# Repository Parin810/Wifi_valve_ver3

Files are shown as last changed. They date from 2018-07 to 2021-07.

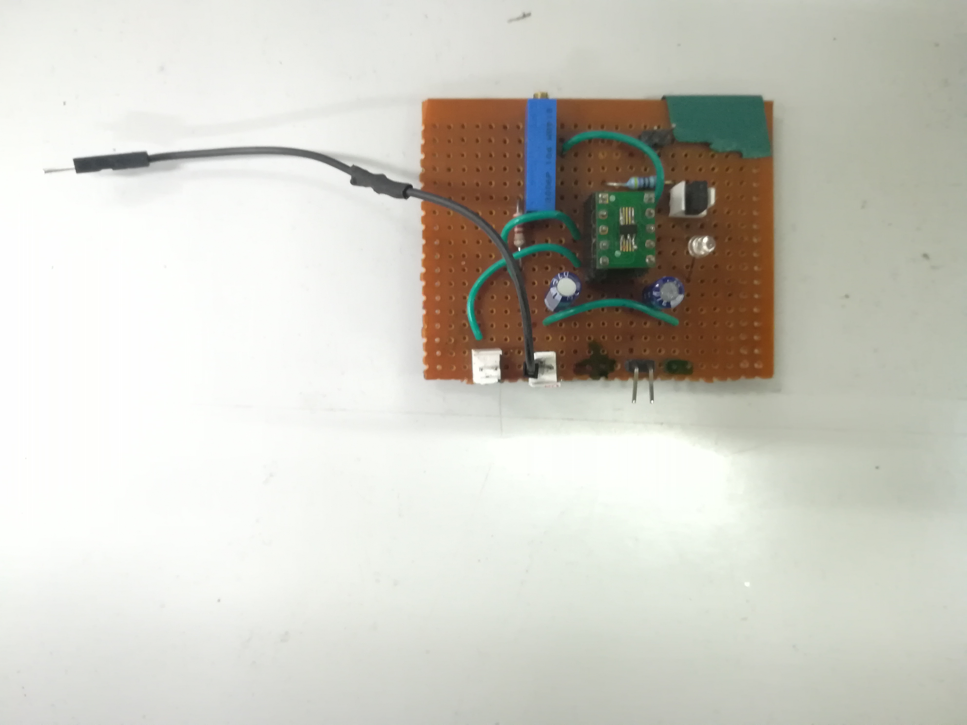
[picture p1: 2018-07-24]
IMG_20180724_112638.jpg

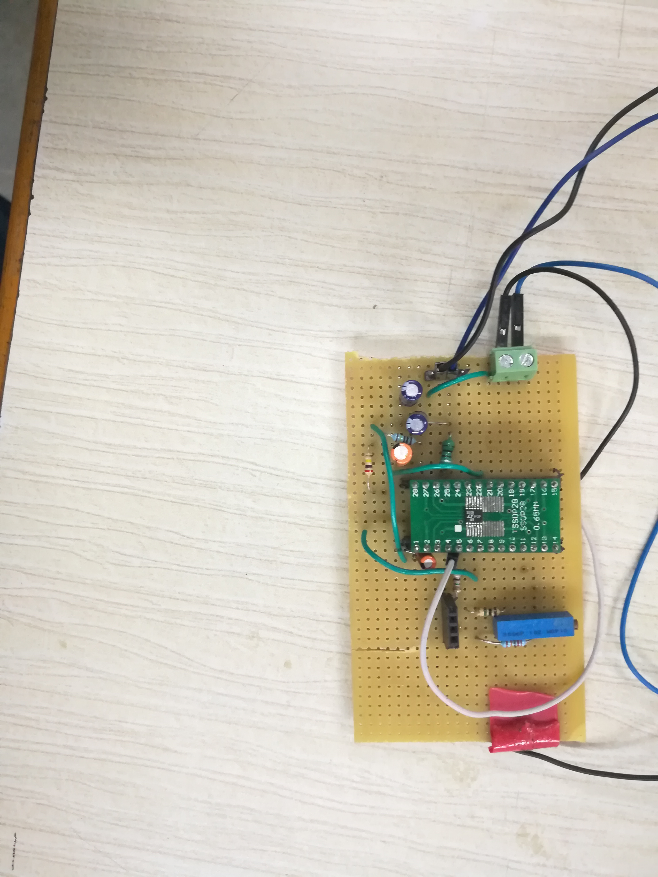
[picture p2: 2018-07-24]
IMG_20180724_134600.jpg

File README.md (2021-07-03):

### Solar Harvesting IoT based Irrigation valve:
This repo contains all the necessary hardware and software information about IoT/Wifi Actuator that has the following features:
1. ESP8266 as the controller/radio chip 
2. Uses MQTT as the communication protocol
3. BQ24210 or MCP73831 based solar harvestor
4. Uses Nodemcu custom build firmware
5. Auto modem sleep enabed (DTIM3,4,5)
6. The valve used is a latching solenoid 
7. DRV8832 as driver for latching solenoid
## Resources
The cheapst SOC that supports IEEE 802.11 standard
[ESP8266](https://tttapa.github.io/ESP8266/Chap04%20-%20Microcontroller.html)

Lua based firmware to simplify application programming
[Nodemcu - Lua](https://nodemcu.readthedocs.io/en/master/)

ESP8266 power consumption
[ESP8266 current profile](https://jeelabs.org/book/1526f/)

## Major Components Used 
(click to see datasheet)

[ESP8266-07](https://www.mikrocontroller.net/attachment/338570/Ai-thinker_ESP-07_WIFI_Module-EN.pdf)

LDO
[AP2112](https://www.diodes.com/assets/Datasheets/AP2112.pdf)

Lipo/ion charger
[MCP73831](http://ww1.microchip.com/downloads/en/DeviceDoc/20001984g.pdf)

Solar lipo/ion charger 
[BQ24210](http://www.ti.com/lit/ds/symlink/bq24210.pdf)

PMOS switch 
[PMV65XP](https://assets.nexperia.com/documents/data-sheet/PMV65XP.pdf)

## Loading LUA firmware
Download Nodemcu flasher from [here](https://github.com/nodemcu/nodemcu-flasher). for windows. For Linux use esptool.py (see repository for details)
Look at this [page](https://nodemcu.readthedocs.io/en/master/en/flash/) from nodemcu lua documentation

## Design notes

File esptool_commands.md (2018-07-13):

Use the follwoing command to flash the 2016 version of the firmware in the ESP8266 Board.

sudo python esptool.py --port /dev/ttyUSB0 write_flash 0x0000 nodemcu_integer_0.9.6-dev_20150704.bin 

Use the follwoing command to flash the 2018 version of the firmware in the ESP8266 Board.

sudo python esptool.py --port /dev/ttyUSB0 write_flash 0x3fc000 esp_init_data_default.bin

sudo python esptool.py --port /dev/ttyUSB0 write_flash 0x0000 nodemcu_master_18_modules_2018_integer.bin

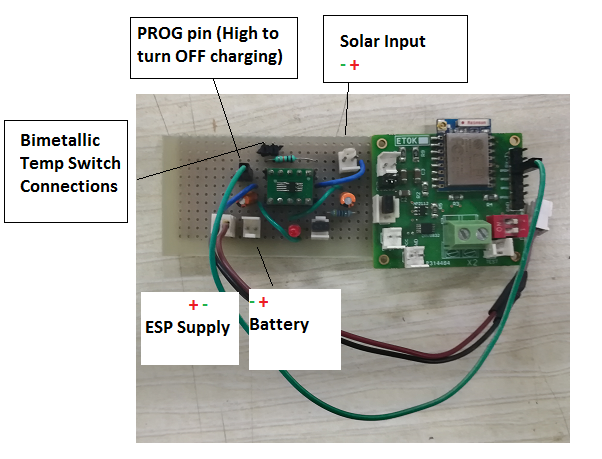
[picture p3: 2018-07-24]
mcp73831_gpb_2.png

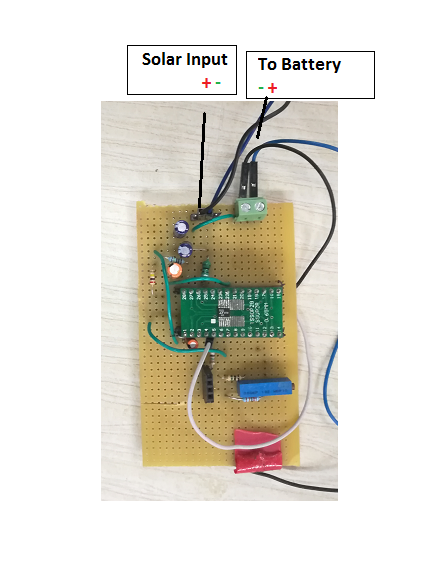
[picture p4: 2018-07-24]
LTC3105_gpb.png

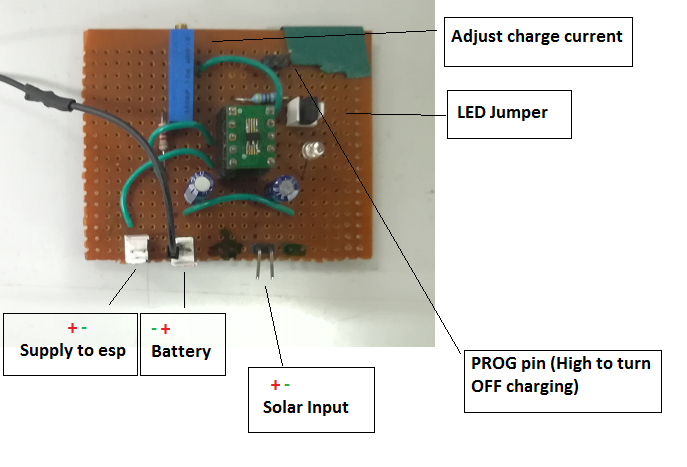
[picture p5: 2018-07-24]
mcp73831_gpb_1.png

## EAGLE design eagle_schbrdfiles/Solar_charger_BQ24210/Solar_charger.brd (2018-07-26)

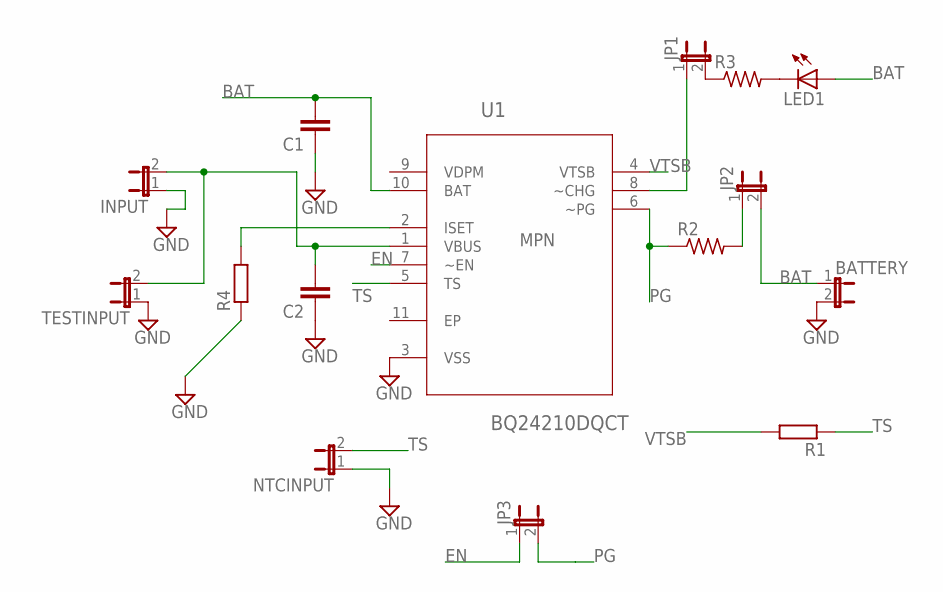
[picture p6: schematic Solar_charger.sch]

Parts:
BATTERY: JP1E; JP1
C1, C2: C2,5-3; C2.5-3
INPUT: JP1E; JP1
JP1, JP2, JP3: JP1E; JP1
LED1: LED5MM
NTCINPUT: JP1E; JP1
R1, R4: R-EU_0204/7; 0204/7
R2, R3: R-US_M1206; M1206
TESTINPUT: JP1E; JP1
U1: BQ24210DQCT; SON50P200X300X80-11N

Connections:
BAT: BATTERY.1, C1.2, JP2.2, LED1.A, U1.10 (BAT)
EN: JP3.1, U1.7 (~EN)
GND: BATTERY.2, C1.1, C2.1, INPUT.1, NTCINPUT.1, R4.1, U1.3 (VSS)
unnamed: C2.2, INPUT.2, TESTINPUT.2, U1.1 (VBUS)
unnamed: R4.2, U1.2 (ISET)
unnamed: JP2.1, R2.2
unnamed: LED1.K (C), R3.2
unnamed: JP1.1, U1.8 (~CHG)
unnamed: JP1.2, R3.1
PG: JP3.2, R2.1, U1.6 (~PG)
TS: NTCINPUT.2, R1.1, U1.5 (TS)
VTSB: R1.2, U1.4 (VTSB)

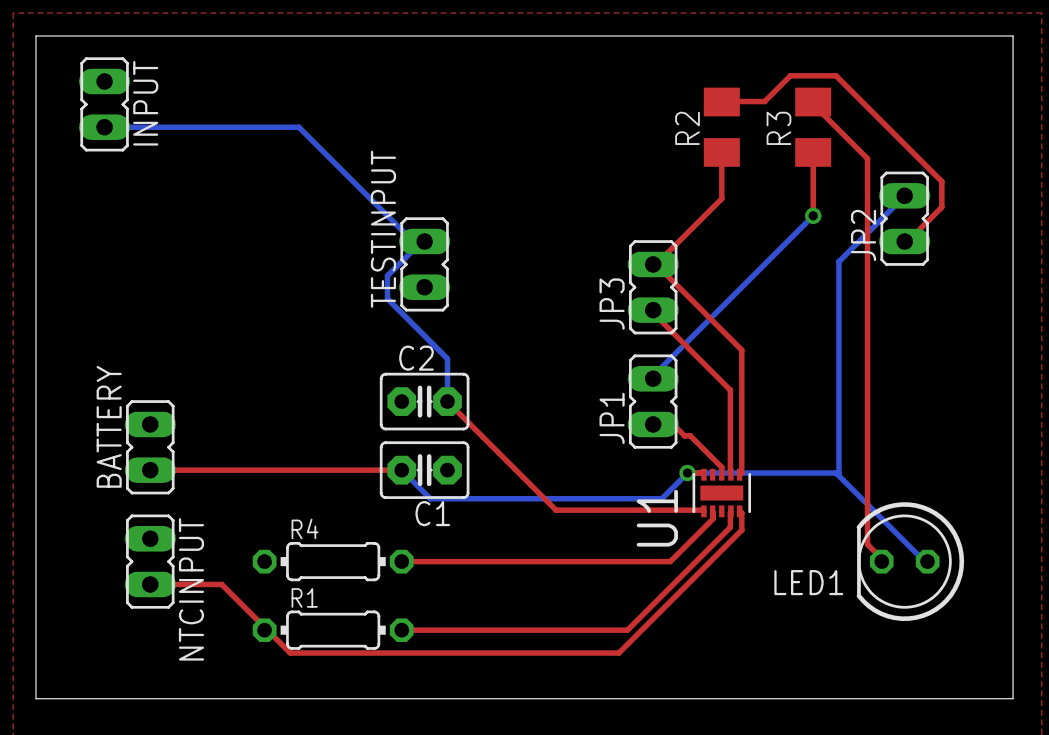
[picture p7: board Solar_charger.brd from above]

Board: 2 copper layers, 54.3 x 36.8 mm, 15 parts (0 on the bottom side), 12 nets.

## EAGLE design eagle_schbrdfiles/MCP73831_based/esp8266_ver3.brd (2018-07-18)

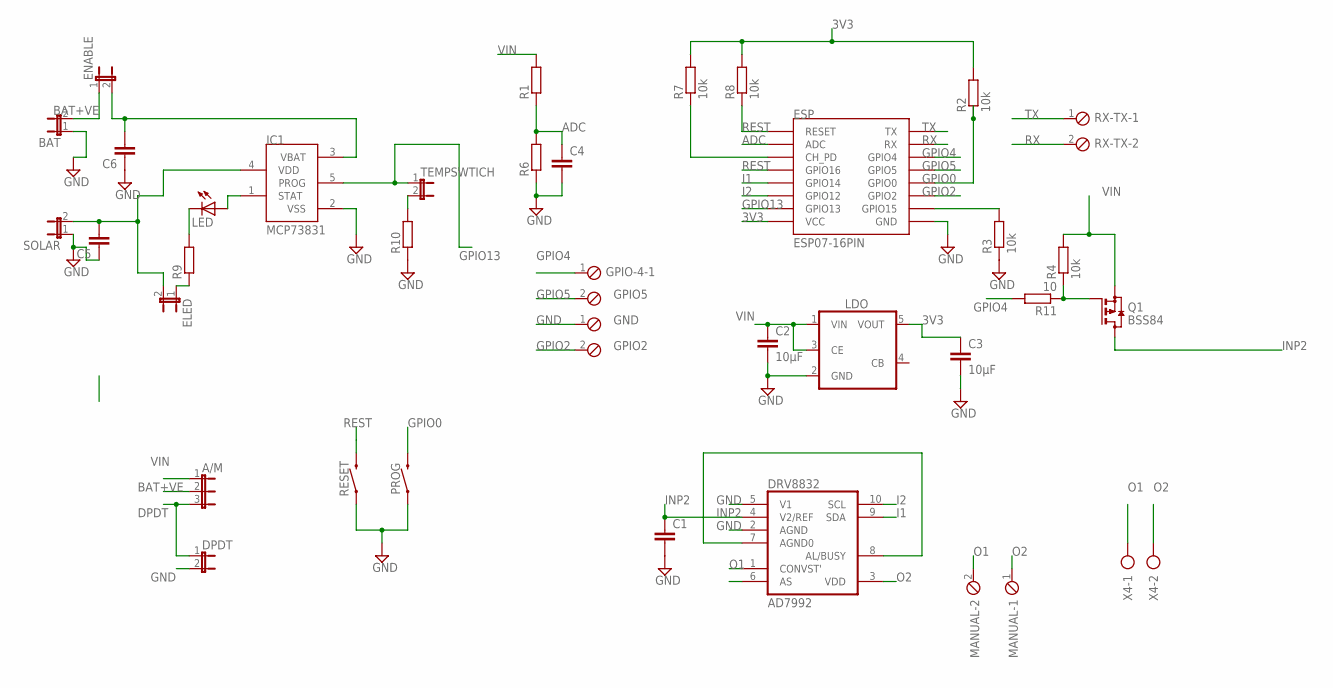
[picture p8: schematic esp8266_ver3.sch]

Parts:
A/M: JP2E; JP2
BAT: JP1E; JP1
C1: C-EUC0805K; C0805K
C2, C3: 10μF; C1206
C4, C5, C6: C-EUC1206; C1206
DPDT: JP1E; JP1
DRV8832: AD7992; MSOP10
ELED: JP1E; JP1
ENABLE: JP1E; JP1
ESP: ESP07-16PIN
GPIO-4: MPT2; 2POL254
IC1: MCP73831; SOT23-5L
LDO: TS5205; SOT25
LED: LED_E; LED_1206
MANUAL: MPT2; 2POL254
PROG: MOMENTARY-SWITCH-SPST-SMD-5.2MM; TACTILE_SWITCH_SMD_5.2MM
Q1: BSS84; SOT23
R1, R6, R9, R10: R-EU_R1206; R1206
R2, R3, R4, R7, R8: 10k; R1206
R11: 10; R1206
RESET: MOMENTARY-SWITCH-SPST-SMD-5.2MM; TACTILE_SWITCH_SMD_5.2MM
RX-TX: MPT2; 2POL254
SOLAR: JP1E; JP1
TEMPSWTICH: JP1E; JP1
X2: MPT2; 2POL254
X4: AK300/2

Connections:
3V3: C3.1, ESP.VCC, LDO.5 (VOUT), R2.2, R7.2, R8.2
ADC: C4.1, ESP.ADC, R1.1, R6.2
B: C6.2, ENABLE.2, IC1.3 (VBAT)
BAT+VE: A/M.2, BAT.2, ENABLE.1
DPDT: A/M.3, DPDT.1
GND: BAT.1, C1.2, C2.2, C3.2, C4.2, C5.1, C6.1, DPDT.2, DRV8832.2 (AGND), DRV8832.5 (V1), ESP.GND, IC1.2 (VSS), LDO.2 (GND), PROG.1, R3.1, R6.1, R10.1, RESET.1, SOLAR.1, X2.1
GPIO0: ESP.GPIO0, PROG.3 (2), R2.1
GPIO2: ESP.GPIO2, X2.2
GPIO4: ESP.GPIO4, GPIO-4.1, R11.2
GPIO5: ESP.GPIO5, GPIO-4.2
GPIO13: ESP.GPIO13, IC1.5 (PROG), TEMPSWTICH.1
I1: DRV8832.9 (SDA), ESP.GPIO14
I2: DRV8832.10 (SCL), ESP.GPIO12
INP2: C1.1, DRV8832.4 (V2/REF), Q1.3 (D)
unnamed: IC1.1 (STAT), LED.A
unnamed: DRV8832.7 (AGND0), DRV8832.8 (AL/BUSY)
unnamed: R10.2, TEMPSWTICH.2
unnamed: LED.C, R9.2
unnamed: ELED.1, R9.1
unnamed: Q1.1 (G), R4.1, R11.1
unnamed: C5.2, ELED.2, IC1.4 (VDD), SOLAR.2
unnamed: ESP.CH_PD, R7.1
unnamed: ESP.GPIO15, R3.2
O1: DRV8832.1 (CONVST'), MANUAL.2, X4.1
O2: DRV8832.3 (VDD), MANUAL.1, X4.2
REST: ESP.GPIO16, ESP.REST (RESET), R8.1, RESET.3 (2)
RX: ESP.RX, RX-TX.2
TX: ESP.TX, RX-TX.1
VIN: A/M.1, C2.1, LDO.1 (VIN), LDO.3 (CE), Q1.2 (S), R1.2, R4.2

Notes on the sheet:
GPIO5
GND
GPIO2

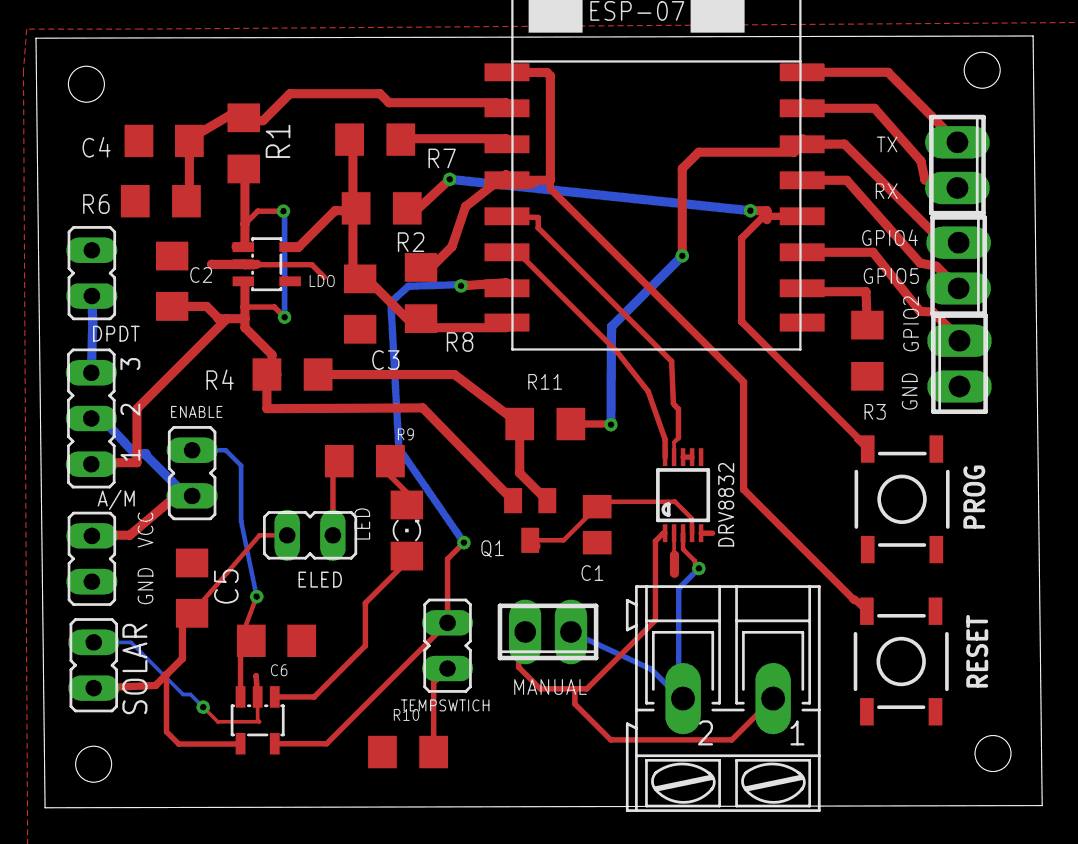
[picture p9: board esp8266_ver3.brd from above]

Board: 2 copper layers, 55.9 x 42.9 mm, 36 parts (0 on the bottom side), 29 nets.

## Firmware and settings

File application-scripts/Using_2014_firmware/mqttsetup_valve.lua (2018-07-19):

--creating client with the macid as the client id 
m = mqtt.Client(wifi.sta.getmac(),60)   --10sec keep alive
--lwt function sends the last will and testament message to tbe sent to the broker in case it goes offline
--m:lwt('lwt','offline',0,0)    

--mqtt offline function keeps checking whether the device has gone offline or not
m:on('offline',function(con) c = false end) 
-- on publish message receive event print the topic and data and do the task
m:on('message', function(conn, topic, data)
  print(topic .. ':')
  if topic == 'esp/'..macid..'/irrigate' then
	irrigate(data)
  end
  if data ~= nil then
    print(data)
  end 
-- Use the data to turn the valve ON or OFF 
 if topic == 'esp/'..macid then
   if data == "1" then 
    startValve() 
  elseif data == "0" then 
    stopValve()
--to give the user the battery status 
  elseif data == "2" then   
    -- paylaod format identifier,bat3,bat6
    payload='1,'..tostring(bat3)..','..tostring(adc.read(0))
    m:publish('esp/'..macid..'/battery',payload,0,0, function(conn) end)
    print("Battery status sent ")  
  elseif data =="3" then 
	print ("sleep")
    node.dsleep(sleepTime)
   else
  end
end
end)

function startValve()
	gpio.mode(pin4,gpio.OUTPUT) --control battery charging
	gpio.write(pin4,gpio.LOW)
	gpio.mode(pin13,gpio.OUTPUT)
	gpio.write(pin13,gpio.LOW)
	tmr.delay(1000)
    gpio.write(pin12,gpio.HIGH)
    gpio.write(pin14,gpio.LOW)

    tmr.alarm(2,80,0,function()
	     gpio.write(pin12,gpio.LOW)
	     gpio.write(pin14,gpio.LOW)
    end)
    gpio.write(pin4,gpio.HIGH)
end


function irrigate(r_time)
	Time = 1000000*30*r_time
	startValve()
	tmr.stop(0)
	wifi.sta.disconnect()
	print("sleep")
	node.dsleep(Time)
end

function stopValve()
	gpio.mode(pin4,gpio.OUTPUT) --control battery charging
	gpio.write(pin4,gpio.LOW)
	gpio.mode(pin13,gpio.OUTPUT)
	gpio.write(pin13,gpio.LOW)
	tmr.delay(1000)
    gpio.write(pin14,gpio.HIGH)
    gpio.write(pin12,gpio.LOW)

     tmr.alarm(2,80,0,function()
	     gpio.write(pin12,gpio.LOW)
	     gpio.write(pin14,gpio.LOW)
     end)
	 --gpio.mode(pin4,gpio.INPUT)
	gpio.write(pin4,gpio.HIGH)
end

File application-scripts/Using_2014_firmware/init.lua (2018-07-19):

ssid='ERTS LAB 101'
password='balstre101'


--configure gpio pins according to revised pin map
pin14 = 5
pin12 = 6
pin4 = 1
pin5 = 2
pin13 = 7

gpio.mode(pin14,gpio.OUTPUT) --in1 as output
gpio.mode(pin12,gpio.OUTPUT) --in2 as output
--

gpio.mode(pin13,gpio.OUTPUT) --control battery charging
gpio.write(pin13,gpio.HIGH)

gpio.write(pin12,gpio.LOW) --in1 for driver (sleep mode)
gpio.write(pin14,gpio.LOW) --in2 for driver (sleep mode)



node.setcpufreq(node.CPU80MHZ) --reduce operating freq for power saving

wifi.setmode(wifi.STATION)

wifi.sta.config(ssid,password)


wifi.sta.connect()

wifiAvailable=0 --initialising the flag 
sleepTime=1000000*60*10   --10 min sleep

dofile('connect1.lua')

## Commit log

2018-07-18 added sch brd files
    [esp8266_ver3.brd, esp8266_ver3.sch]
2018-07-18 added schematic and brd files
    [esp8266_ver3.brd, esp8266_ver3.sch]
2018-07-18 added bom
    [bom.ods]
2018-07-24 added board images
2018-07-26 added eagle schematics
    [Solar_charger.brd, Solar_charger.sch]

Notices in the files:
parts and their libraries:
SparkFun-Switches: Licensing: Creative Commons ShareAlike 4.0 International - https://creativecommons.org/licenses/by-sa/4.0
